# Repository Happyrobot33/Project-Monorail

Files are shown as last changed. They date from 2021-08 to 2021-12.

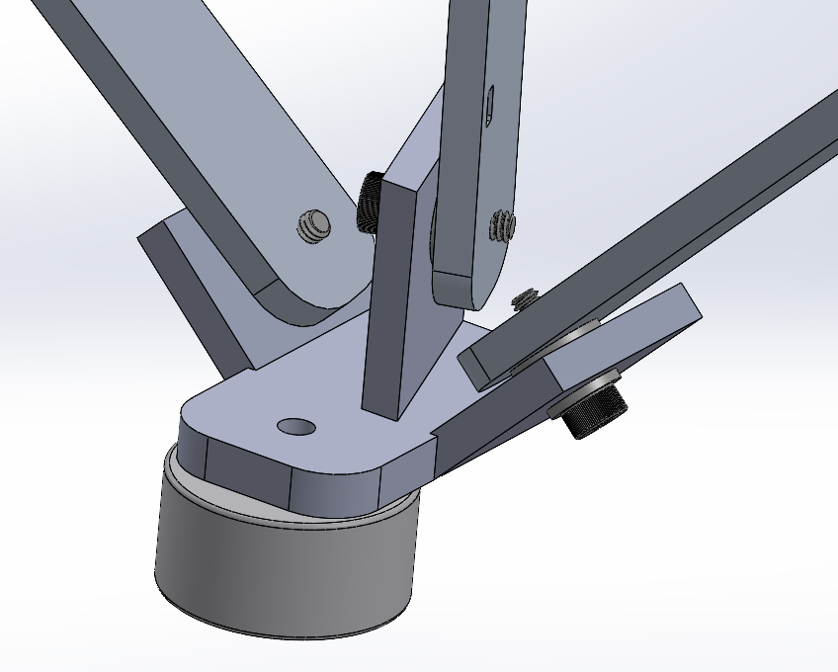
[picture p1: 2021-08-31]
CAD/Development Images/holy fuck.PNG

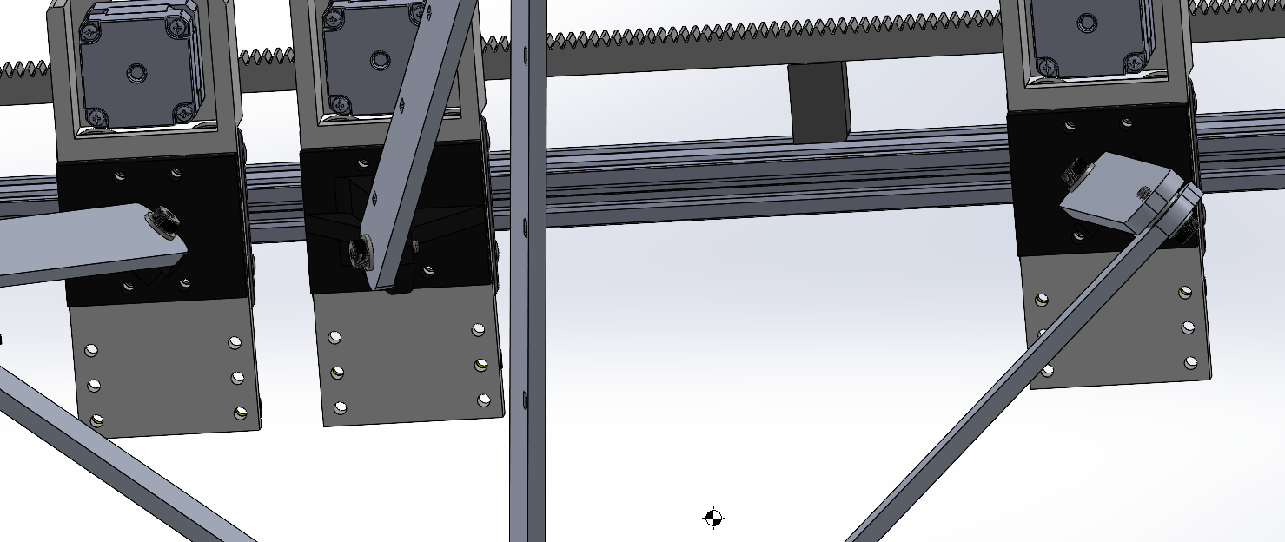
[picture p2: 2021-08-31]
CAD/Development Images/New Mounts.PNG

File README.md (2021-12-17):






# Project-Monorail
Project Monorail is an attempt to recreate a design shown by Nicholas Seward (https://www.youtube.com/watch?v=oBBhVcemVHc&amp;t=26s) that uses 1 linear rail to accomplish 3 dimensional movement

Use this to visualize if a point is reachable or not to prevent issues:
https://editor.p5js.org/Happyrobot33/sketches/HqeGeLe6U

https://user-images.githubusercontent.com/32679887/117662900-11516d00-b16e-11eb-9a66-542f85682d6e.mp4

https://user-images.githubusercontent.com/32679887/118267545-3d306380-b48a-11eb-8856-cf8bc8f9db5a.mp4

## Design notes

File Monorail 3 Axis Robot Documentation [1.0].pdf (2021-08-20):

# Monorail 3 Axis Robot Documentation

## Written and Designed by Matthew Herber

## Index: Pin Reservations Custom Expansion Board Diagram Custom Firmware Command Set Sample Program Basic Code Loop Explanation

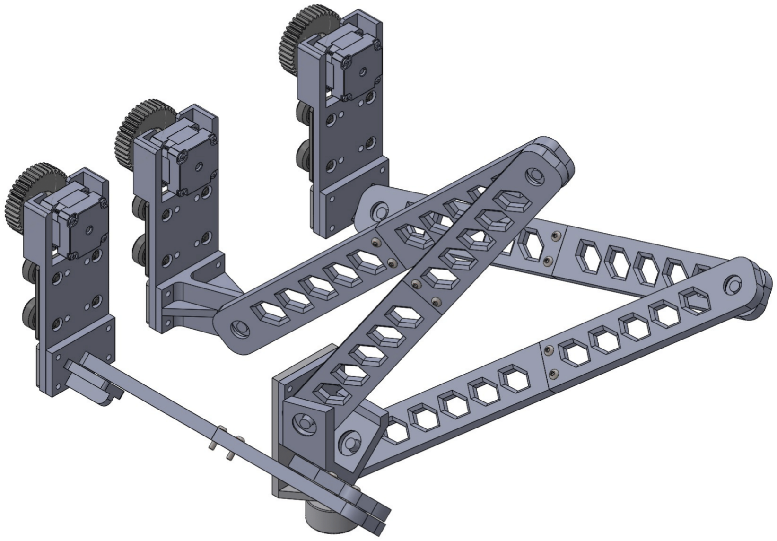
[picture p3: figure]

## REV 1.0 (8/19/2021) Page: 1

## Pin Reservations

Stepper 1
Data: D22, D23, D24, D25
Endstop: D34

Stepper 2
Data: D26, D27, D28, D29
Endstop: D35

Stepper 3
Data: D30, D31, D32, D33
Endstop: D36

Other:
Electromagnet: D37

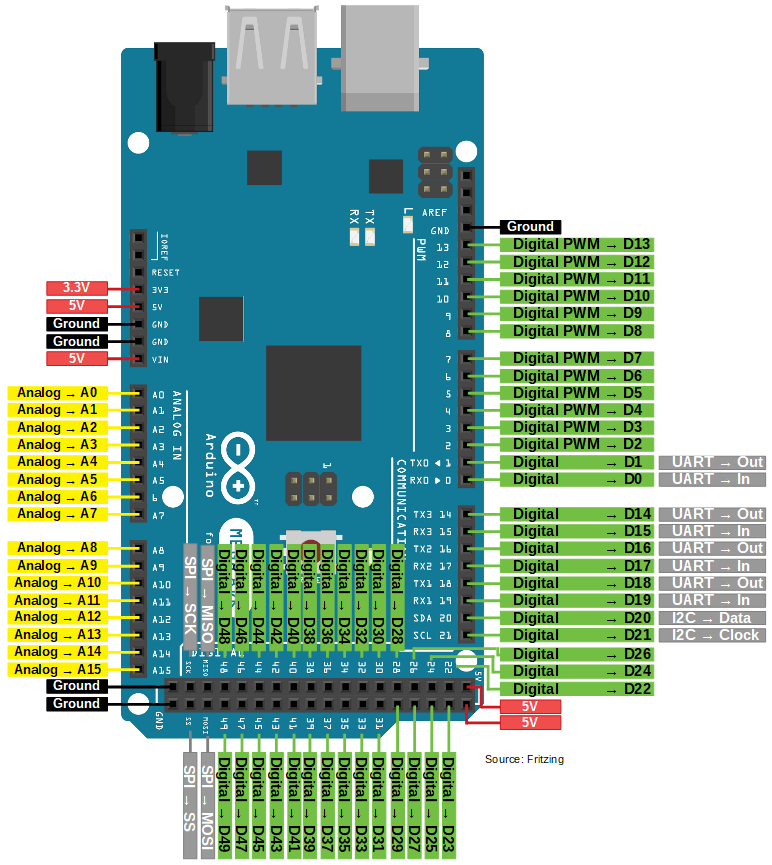
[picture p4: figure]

## REV 1.0 (8/19/2021) Page: 2

## Custom Expansion Board Diagram (Board Revision 3.0)

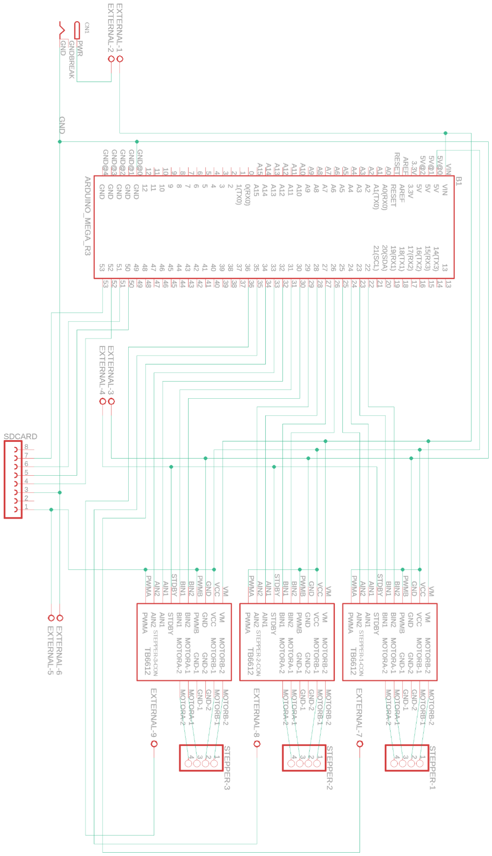
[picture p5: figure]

## REV 1.0 (8/19/2021) Page: 3

## Custom Firmware Command Set

Use # to indicate a comment on said line. To end a line, use ;\. All position commands use MM unless otherwise specified

lmove(x,y,z)
Moves the robot EOAT to the specified X Y Z coordinates in a straight line

jmove(x,y,z)
Moves the robot EOAT to the specified X Y Z coordinates as quick as possible

delay(ms)
Halts program execution for a specified amount of milliseconds

speed(%)
Sets the speed of the robot based on a percentage of the max speed. This change affects all motion moves after it is called

accel(%)
Sets the acceleration of the robot based on a percentage of the max acceleration. This change affects all motion moves after it is called

Carc(x,y,z,r,startAngle,endAngle)
Does a clockwise arc move given a center position, a radius from that center, a start angle and an end angle. always make sure your end angle is larger than your start angle

CCarc(x,y,z,r,startAngle,endAngle)
Does a counter-clockwise arc move given a center position, a radius from that center, a start angle and an end angle. always make sure your end angle is larger than your start angle

EOAT(0/1)
Turns on or off the EOAT, 0 for off and 1 for on

## REV 1.0 (8/19/2021) Page: 4

## Sample Program

### String program = "\ #basic starting program for testing;\ jmove(550,200,100);\ delay(1000);\ jmove(50,50,25);\ jmove(500,50,5);\ jmove(200,100,100);\ jmove(0,0,0);\ delay(1000);\ EOAT(1);\

;\

### Section to test speed command;\ speed(20);\ lmove(300,200,300);\ speed();\ lmove(0,0,0);\ EOAT(0);\

;\

### Section to test accel command;\ delay(1000);\ accel(5);\ lmove(300,200,300);\ accel();\ lmove(0,0,0);\ delay(1000);\ EOAT(1);\ #Rapid section testing individual axis moves;\

#X;\

### lmove(200,0,0);\ delay(1000);\ jmove(100,0,0);\

## REV 1.0 (8/19/2021) Page: 5

## Sample Program (cont)

#Y;\

### lmove(100,100,0);\ delay(1000);\ jmove(100,0,0);\

#Z;\

### lmove(100,0,100);\ delay(1000);\ jmove(100,0,0);\ #ALL AXIS;\ lmove(400,50,200);\ delay(1000);\ jmove(100,0,0);\ #Arc Testing;\ Carc(400,200,0,200,360,0);\ lmove(0,0,0);\ CCarc(400,200,0,200,0,360);\ lmove(0,0,0);\ EOAT(0);\

";

## REV 1.0 (8/19/2021) Page: 6

## Basic Code Loop Explanation

The execution of the custom firmware is actually quite simple. There is a string variable stored internally to the code, that contains the entire program. This is done so that in later revisions strings can be read in from a storage device to have different programs stored without requiring a reflash of the Arduino itself. This string is then converted into an array of instructions, using ;\ as a line end marker. This array is looped over for each instruction.

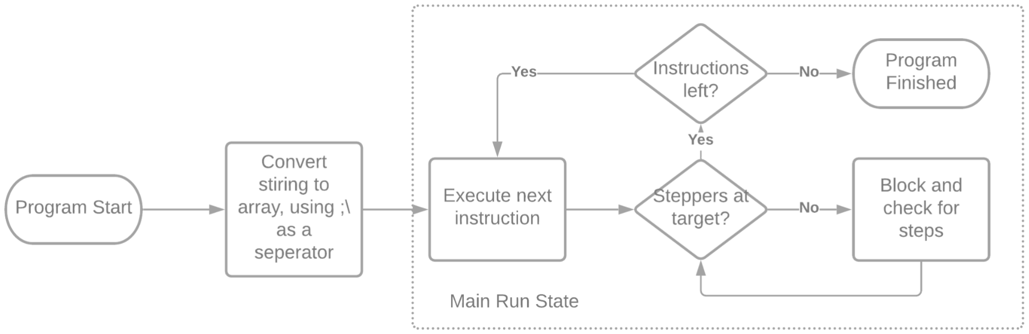
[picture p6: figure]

## REV 1.0 (8/19/2021) Page: 7

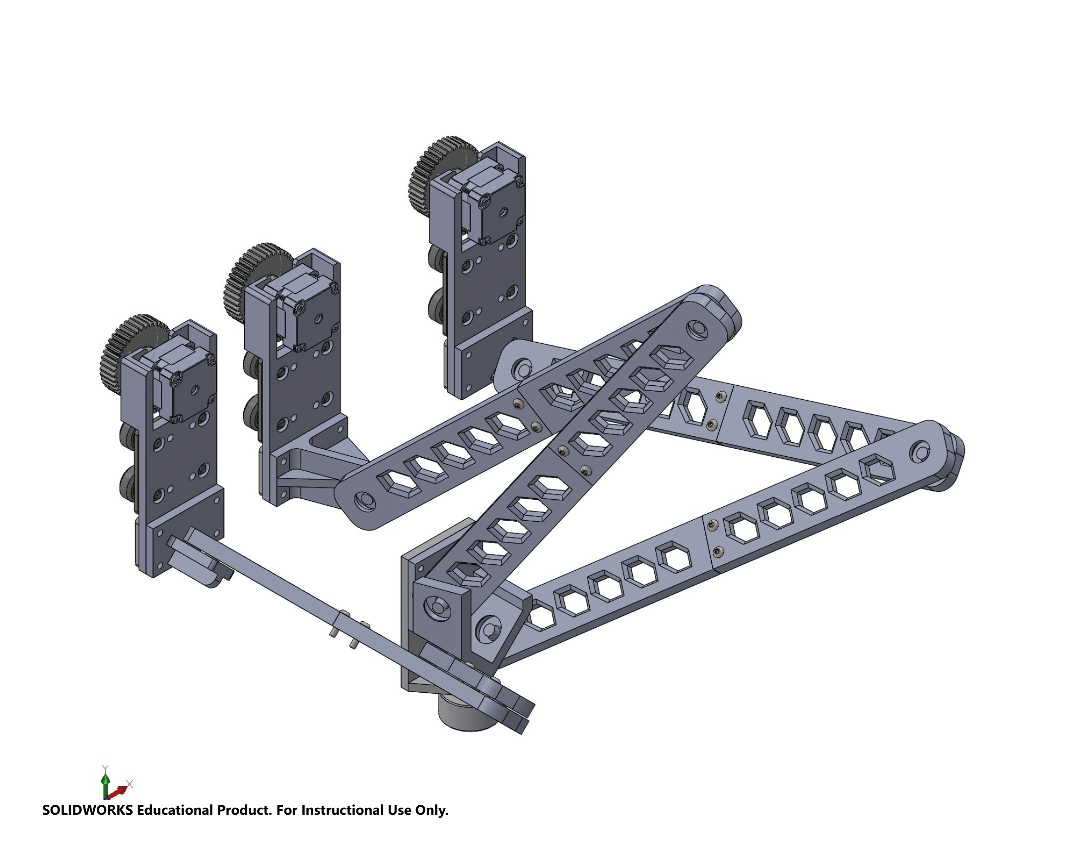
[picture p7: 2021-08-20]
Cover Image-1.png

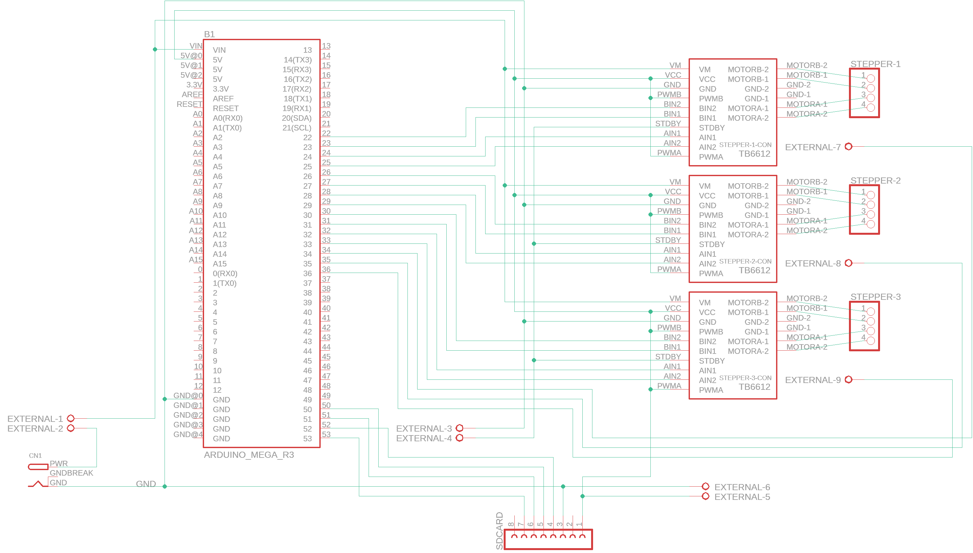
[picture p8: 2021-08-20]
rev 3 diagram.png

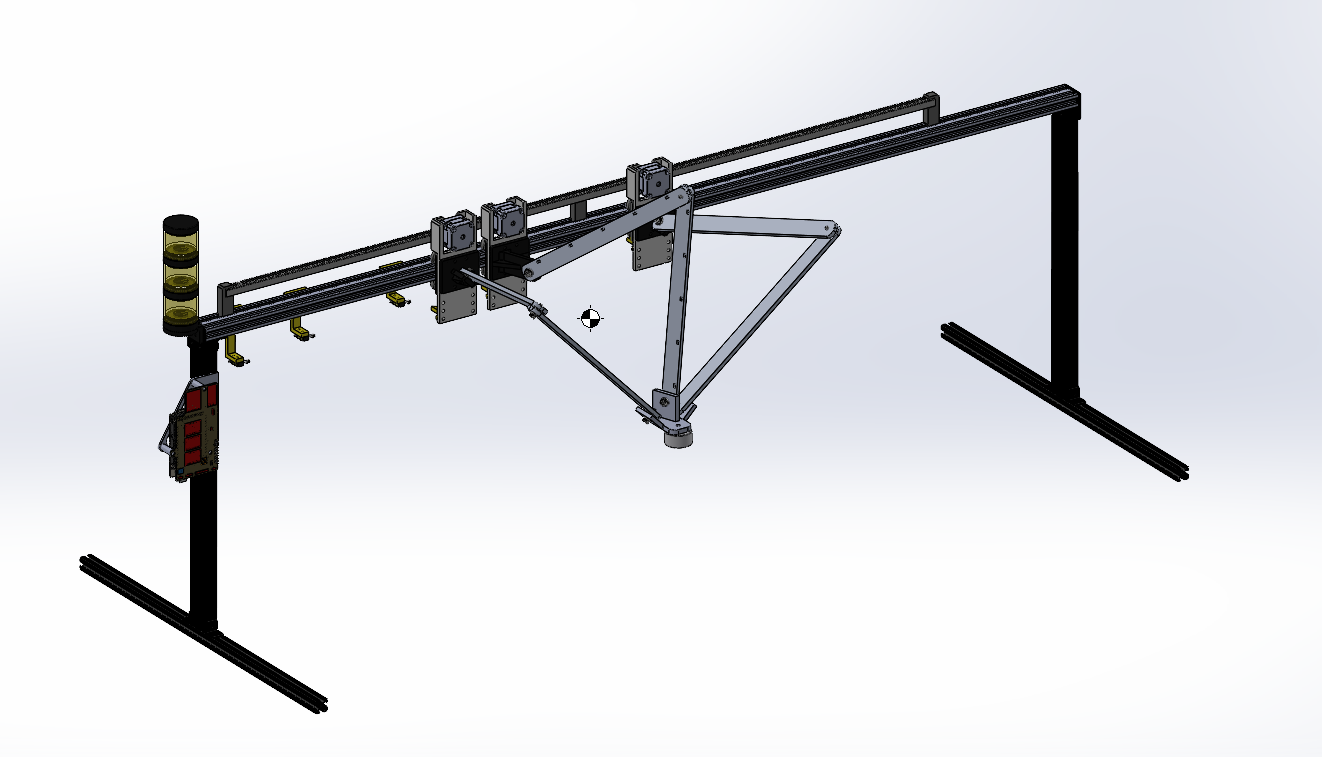
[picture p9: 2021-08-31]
CAD/Development Images/Full Image.PNG

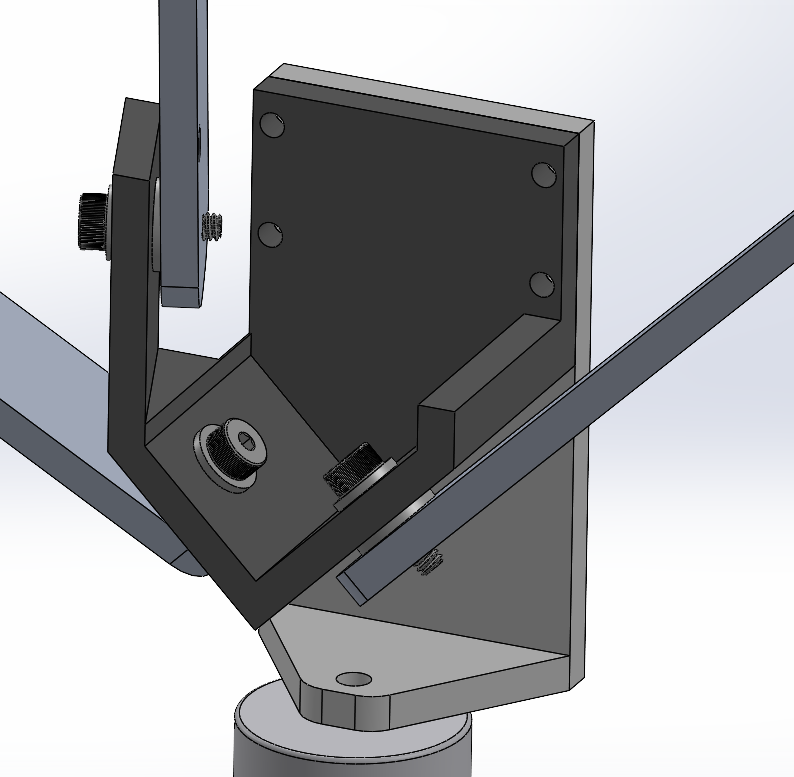
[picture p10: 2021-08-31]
CAD/Development Images/help.PNG

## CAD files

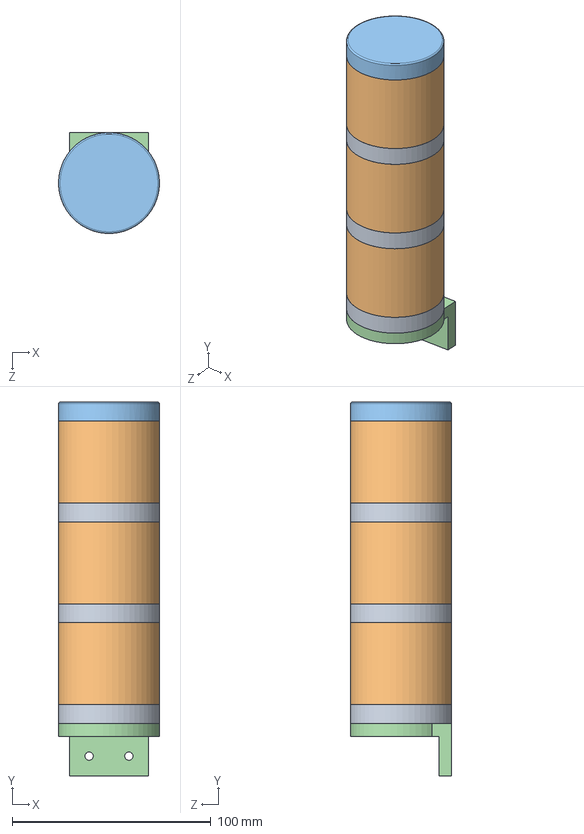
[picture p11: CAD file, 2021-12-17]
CAD/A600 Misc/Light Stack.SLDASM
50.8 x 188.3 x 50.8 mm
Light Stack Seperator x 3
Light Stack Diffuser x 3
Light Stack Cap
Light Stack Base

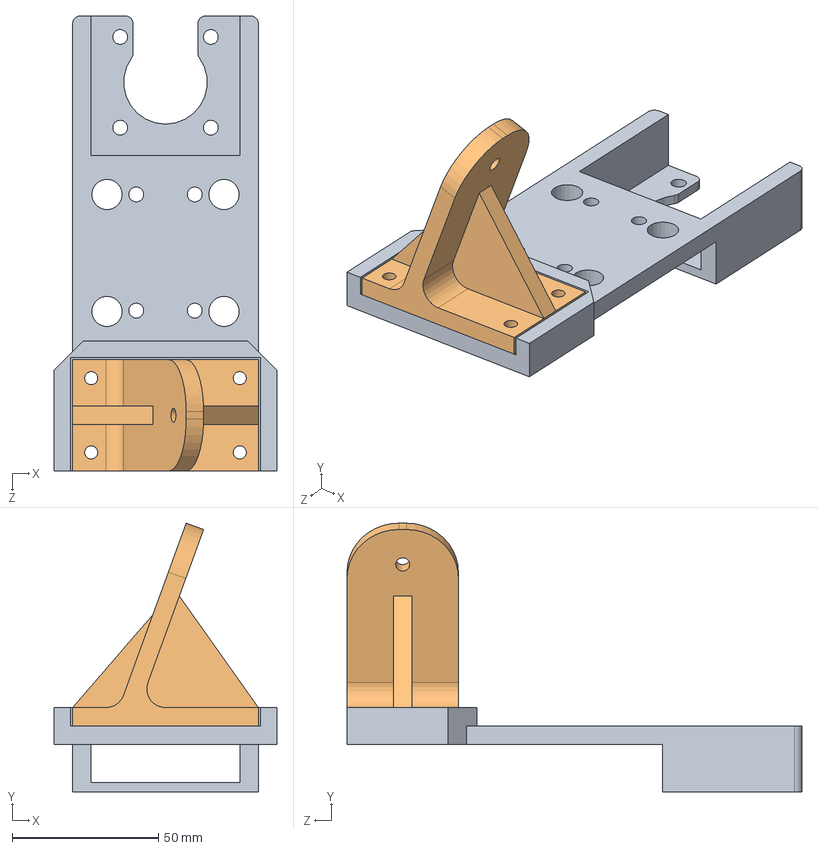
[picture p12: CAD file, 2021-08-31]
CAD/FEA Assembly.SLDASM
76.2 x 91.9 x 155.6 mm
Slide Casing
Inner Mount

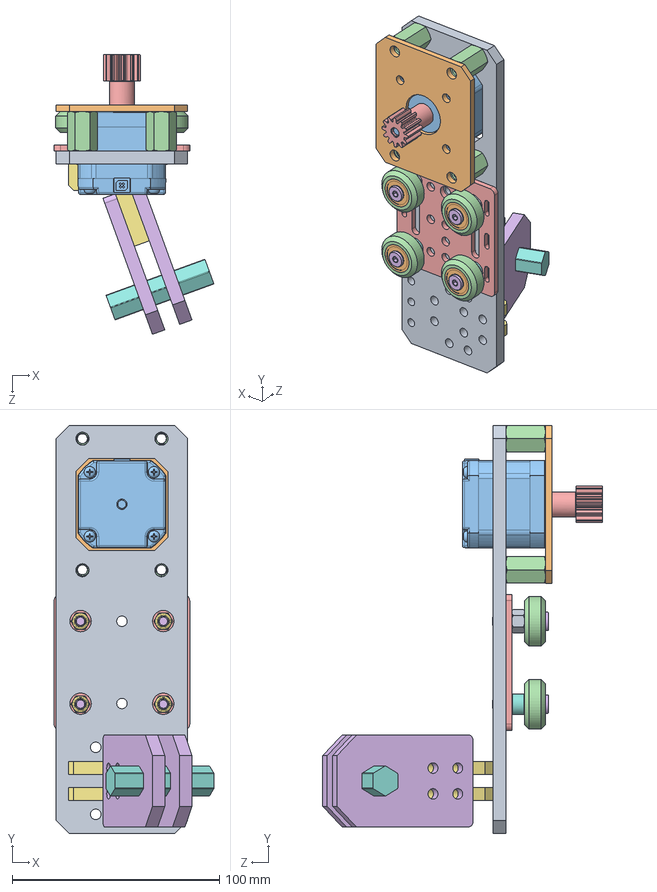
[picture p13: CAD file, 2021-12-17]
CAD/A200 Cart/A200 Cart.SLDASM
77.1 x 196.8 x 134.9 mm
A201 Cart Mount Plate
A202 Cart Stepper Plate
6627T67_Position-Control DC Motor
91780A357_Female Threaded Hex Standoff x 4
V-Slot Gantry Plate 20mm.step
Low Profile Screw M5 v1.step x 4
Nylon Insert Lock Nut M5.step x 4
Aluminum Spacer 6mm.step x 2
Eccentric Spacer 6mm v1.step x 2
Ball Bearing 5 x 16 x 5.step x 8
Precision Shim 8 x 5 x 1.step x 4
Xtreme Solid V Wheel.step x 4
5172T160_HT-LOAD MTL GEAR--20 DEG PRESSURE ANGLE
A204 Outer Mount Bearing Plate x 2
A203 Inner Mount Angle Bracket x 2
1_2 OD Hex Stock (18) (217-3309)^A200 Cart

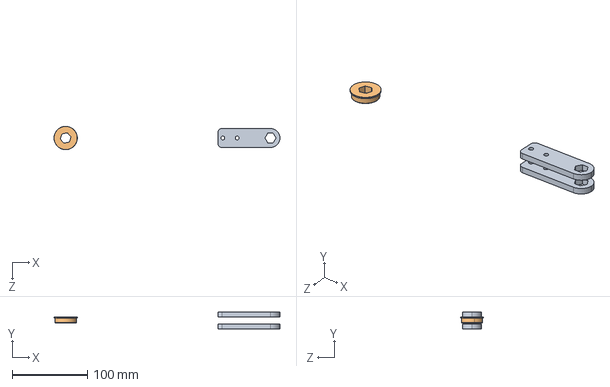
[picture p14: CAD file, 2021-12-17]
CAD/A400 Link/A400 Link.SLDASM
301.3 x 22.2 x 31.1 mm
A402 Bar Clevis Plate x 2
am-2986 FR8ZZ Hex Bearing.step

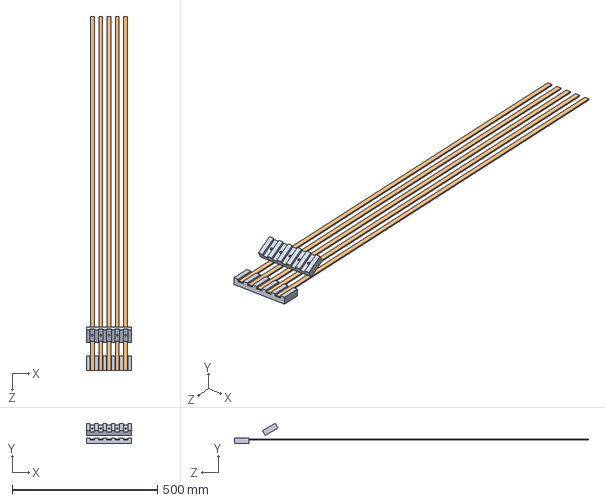
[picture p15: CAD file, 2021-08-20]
CAD/A300 Rail/Bus Bar Concept.SLDASM
155.6 x 70.5 x 1219.2 mm
Bus Bar Holder x 2
Copper Bus Bar x 5

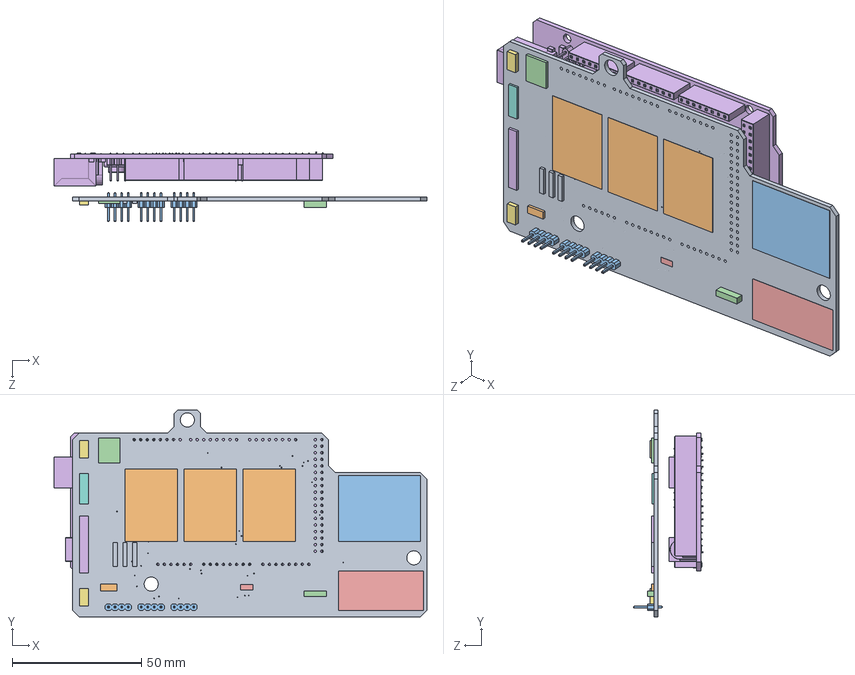
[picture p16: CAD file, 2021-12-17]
CAD/A600 Misc/Board.SLDASM
144.3 x 80.0 x 26.9 mm
Board.step
TB6612-BREAKOUT-MOTOR-CONTROLLER.step x 3
1X04.step x 3
DCJACK_2MM_PTH.step
NRF24L01_RF_MODULE.step
W237-5P.step
W237-132.step x 2
W237-3E.step
220 Ω.step x 3
2N2222.step
MICRO_SD_BREAKOUT.step
F_QMX.step
CLEAR.step
ArduinoMega_IGES.igs

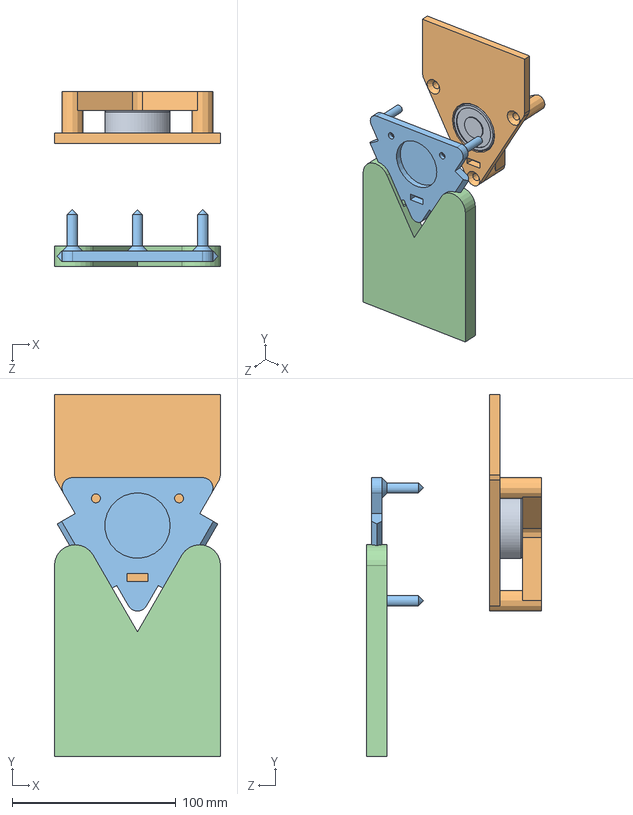
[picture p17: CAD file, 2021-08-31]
CAD/A500 Head/ATC Example Usage.SLDASM
101.6 x 221.3 x 107.2 mm
25kg electromagnet
ATC
ATC Tool Mount
ATC Tool Holder

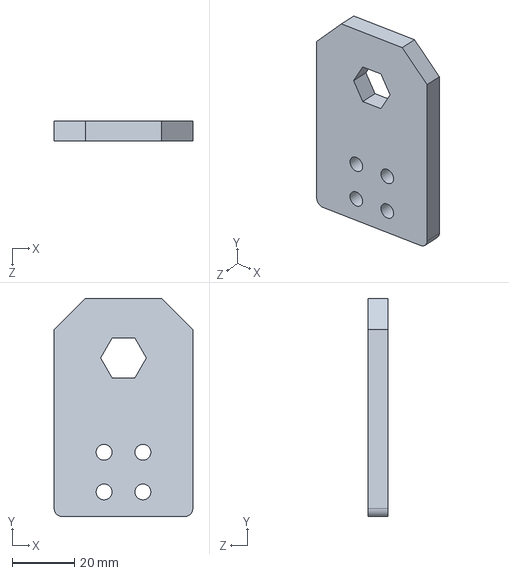
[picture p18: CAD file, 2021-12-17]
CAD/A200 Cart/A204 Outer Mount Bearing Plate.SLDPRT
44.5 x 69.8 x 6.35 mm

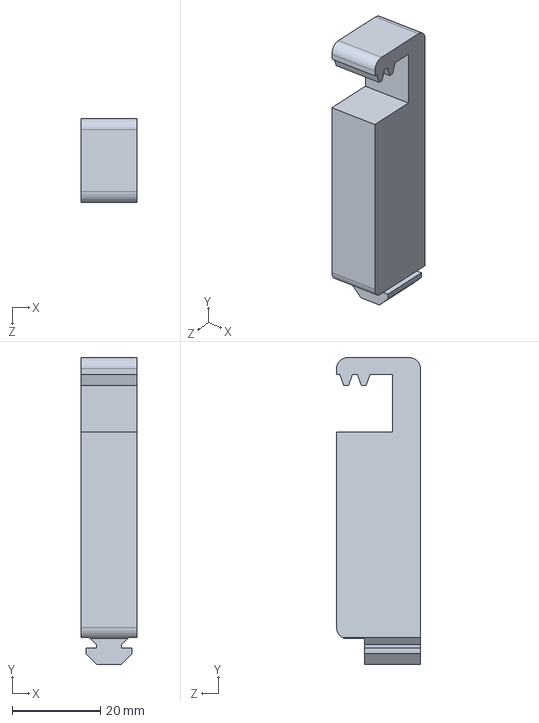
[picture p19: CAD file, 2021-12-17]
CAD/A300 Rail/Temporary Gear Mount.SLDPRT
12.7 x 69.6 x 19.1 mm

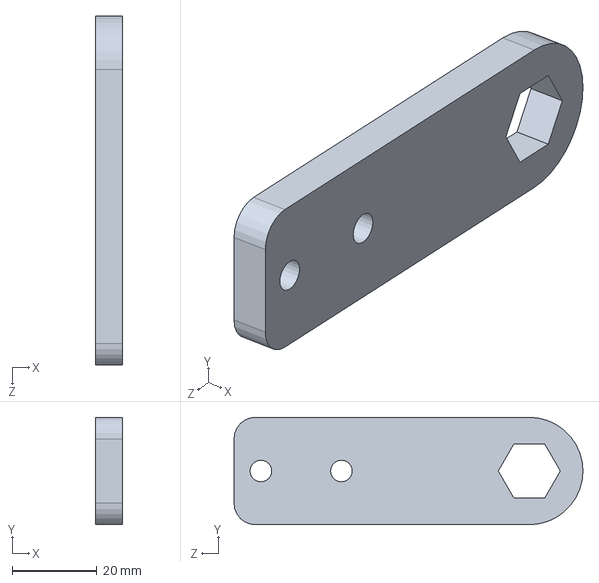
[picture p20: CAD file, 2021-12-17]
CAD/A400 Link/A402 Bar Clevis Plate.SLDPRT
6.35 x 25.4 x 82.5 mm

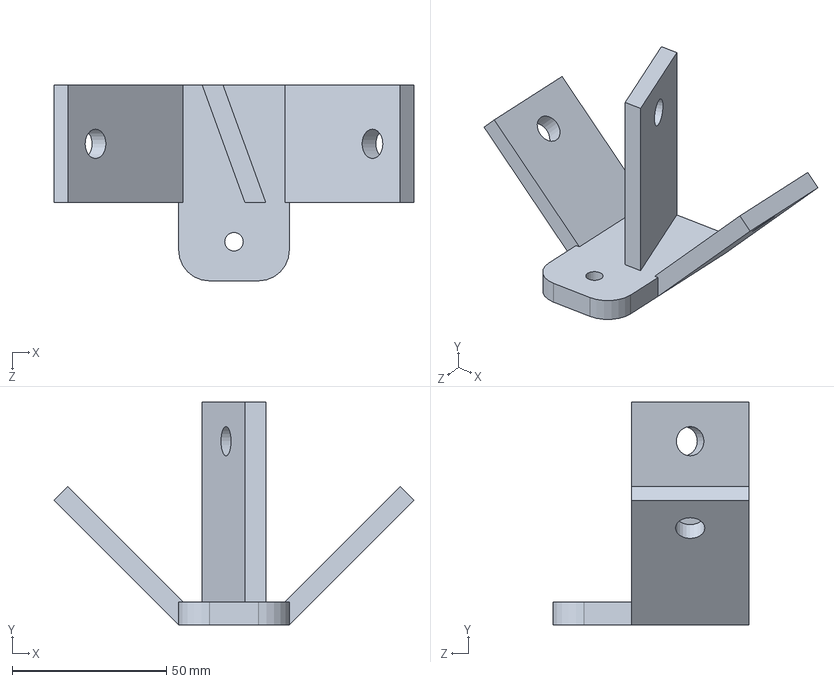
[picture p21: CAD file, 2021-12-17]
CAD/A500 Head/Head v2.SLDPRT
116.7 x 72.3 x 63.5 mm

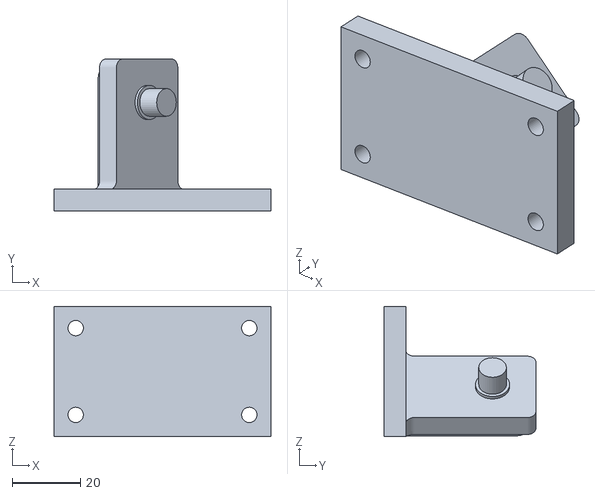
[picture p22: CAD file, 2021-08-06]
STL/Outer Mounts Default.STL
63.5 x 44.5 x 38.1

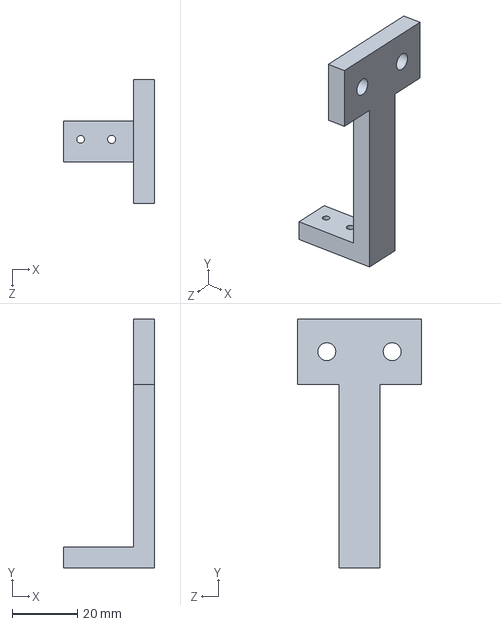
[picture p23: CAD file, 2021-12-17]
CAD/A300 Rail/MicroSwitch Under Mount.SLDPRT
27.8 x 76.2 x 38.1 mm

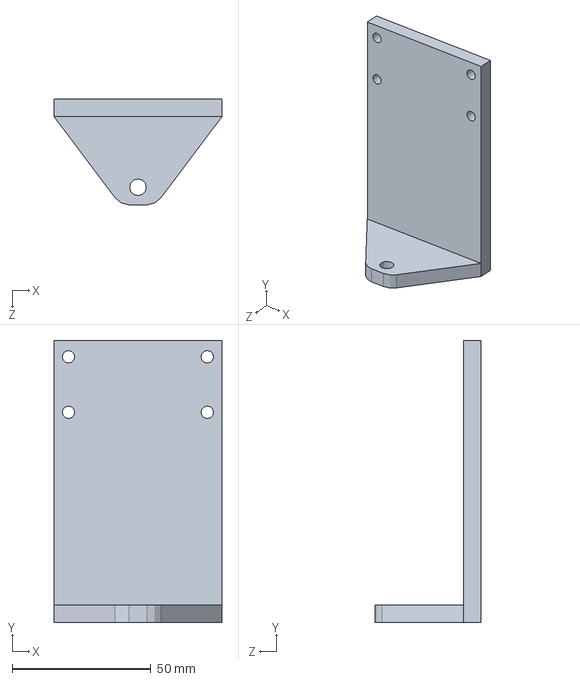
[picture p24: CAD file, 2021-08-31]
CAD/A500 Head/Electromagnet EOAT.SLDPRT
60.5 x 101.6 x 38.1 mm

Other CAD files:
Render/Head.PLY
CAD/A600 Misc/Light Stack Diffuser.SLDPRT
CAD/Triangle Calculations.SLDPRT
Render/Extrusion.PLY
CAD/A200 Cart/A201 Cart Mount Plate.SLDPRT
CAD/A200 Cart/A202 Cart Stepper Plate.SLDPRT
CAD/A200 Cart/A203 Inner Mount Angle Bracket.SLDPRT
CAD/A200 Cart/Cart Mount Plate.DXF
CAD/A200 Cart/Cart Stepper Plate.DXF
CAD/A200 Cart/Inner Mount Angle Bracket.DXF
CAD/A200 Cart/Outer Mount Bearing Plate.DXF
CAD/A300 Rail/Bus Bar Holder.SLDPRT
CAD/A300 Rail/Copper Bus Bar.SLDPRT
CAD/A400 Link/A401 Aluminum Bar.SLDPRT
CAD/A400 Link/Bar Clevis Plate.DXF
CAD/A500 Head/ATC Tool Holder.SLDPRT
CAD/A500 Head/ATC Tool Mount.SLDPRT
CAD/A500 Head/ATC.SLDPRT
CAD/A500 Head/Head.SLDPRT
CAD/A600 Misc/Board Mount.SLDPRT
CAD/A600 Misc/Light Stack Base.SLDPRT
CAD/A600 Misc/Light Stack Cap.SLDPRT
CAD/A600 Misc/Light Stack Seperator.SLDPRT
CAD/OLD/Bar.SLDPRT
CAD/OLD/Bearing Fit Test Internal.SLDPRT
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

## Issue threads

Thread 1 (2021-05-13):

No arc commands

Happyrobot33, 2021-05-13:
No arc / circle commands are present. Here is a proposal for that: https://www.desmos.com/calculator/zzamiibnki

Happyrobot33, 2021-05-14:
Arc commands added in fff759550248dae4620b4c08fd9e4bcf71ba2048, but issues are still present so this is still a problem. commands disabled in a52cebe1a37ab307f21e28994de08a783c661ccf. Plan to fix in coming days

Happyrobot33, 2021-05-18:
Arc commands seem to work, however due to #2, if this is true or not is currently unknown

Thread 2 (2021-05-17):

Very jittery and y axis is very imprecise

Happyrobot33, 2021-05-17:
This is likely due to multiple factors adding up on eachother, for one being the current arms are only 7 inches long. another is that the arms are quite thin, and the mounts also have alot of give. hoping to fix these things soon.

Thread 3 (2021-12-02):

Gear Rack Mount not final version

Happyrobot33, 2021-12-02:
Current Gear rack mounting solution does not allow for additional racks. Final version should use something that allows for additional racks to be added

Happyrobot33, 2022-10-31:
Solved with gear rack being moved to the back

Closed 2022-10-31.

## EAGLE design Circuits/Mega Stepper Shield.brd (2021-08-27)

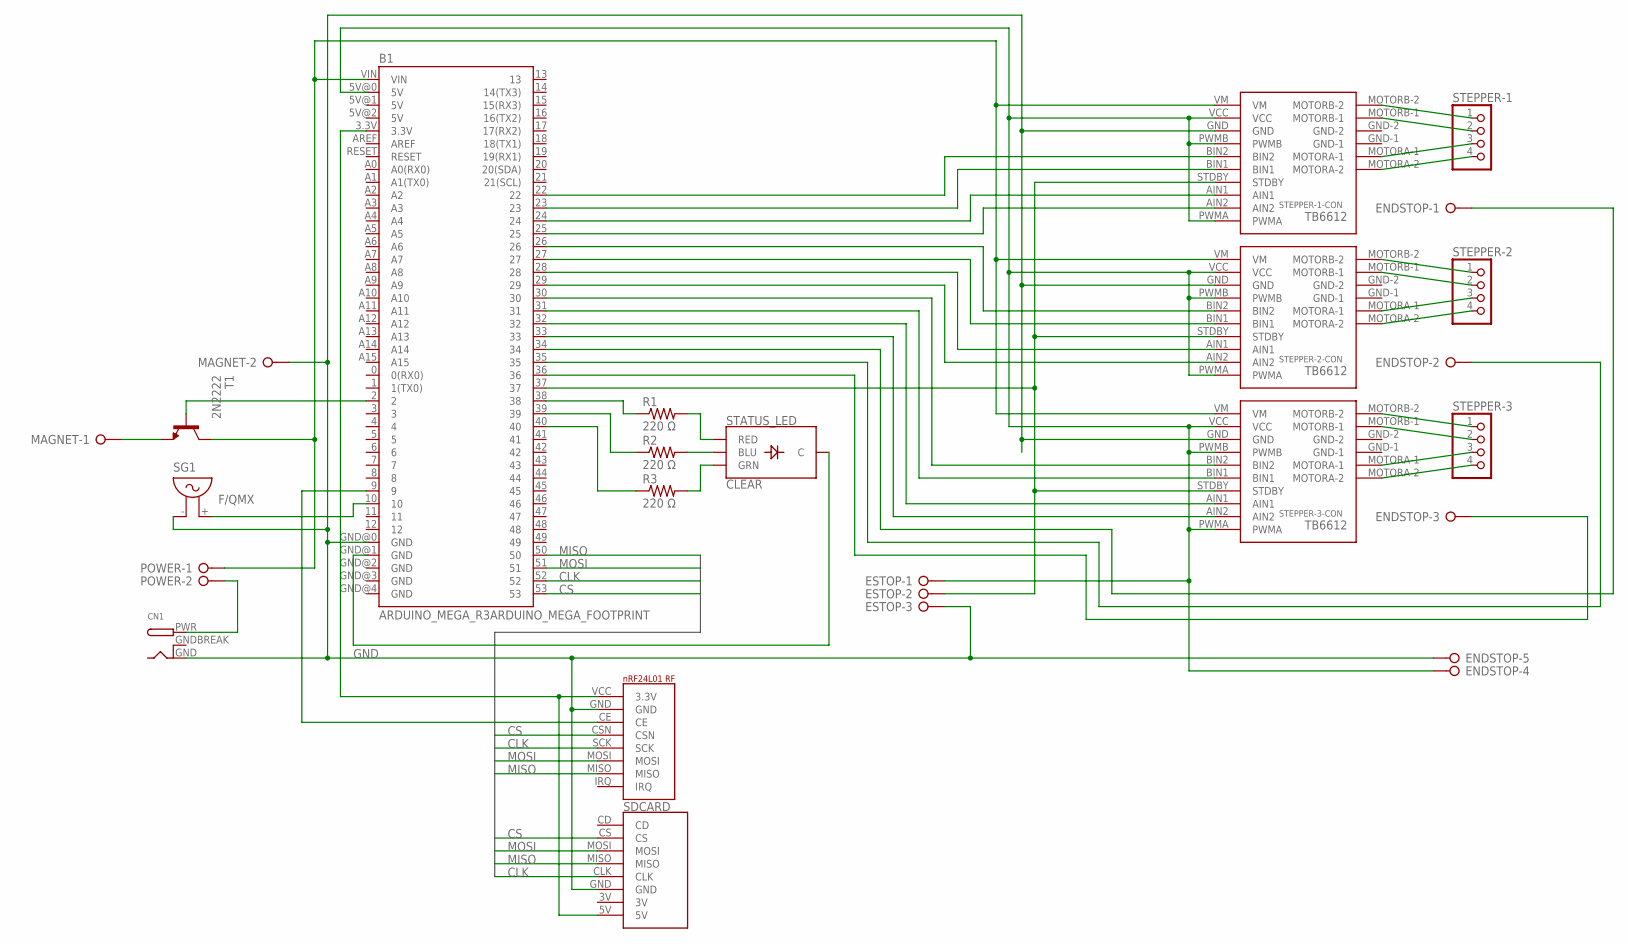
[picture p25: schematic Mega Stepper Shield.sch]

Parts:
B1: ARDUINO_MEGA_R3ARDUINO_MEGA_FOOTPRINT; ARDUINO_MEGA_SHIELD_DIMENSIONLESS
CN1: DCBARRELPTH; DCJACK_2MM_PTH
ENDSTOP: W237-05P; W237-5P
ESTOP: W237-3E
MAGNET: W237-02P; W237-132
POWER: W237-02P; W237-132
R1, R2, R3: 220 Ω; 0204/7
SDCARD: MICRO_SD_BREAKOUT; MICROSDCARDBREAKOUT
SG1: F/QMX
STATUS_LED: CLEAR; LED-RGB-THRU
STEPPER-1, STEPPER-2, STEPPER-3: PINHD-1X4; 1X04
STEPPER-1-CON, STEPPER-2-CON, STEPPER-3-CON: TB6612-BREAKOUT-MOTOR-CONTROLLER; TB6612-HEADERS
T1: 2N2222; TO92-EBC-OVAL
U$1: NRF24L01_RF_MODULE; NRF24L01RF

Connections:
3.3V: B1.3.3V, SDCARD.5V, U$1.VCC (3.3V)
5V: B1.5V@0 (5V), ENDSTOP.4, ESTOP.1, STEPPER-1-CON.PWMA, STEPPER-1-CON.PWMB, STEPPER-1-CON.VCC, STEPPER-2-CON.PWMA, STEPPER-2-CON.PWMB, STEPPER-2-CON.VCC, STEPPER-3-CON.PWMA, STEPPER-3-CON.PWMB, STEPPER-3-CON.VCC
12V10A: B1.VIN, POWER.1, STEPPER-1-CON.VM, STEPPER-2-CON.VM, STEPPER-3-CON.VM, T1.C
AIN1: B1.24, STEPPER-1-CON.AIN1
AIN2: B1.25, STEPPER-1-CON.AIN2
BIN2: B1.22, STEPPER-1-CON.BIN2
CLK: B1.52, SDCARD.CLK, U$1.SCK
CS: B1.53, SDCARD.CS, U$1.CSN
GND: B1.GND@0 (GND), CN1.GND, ENDSTOP.5, ESTOP.3, MAGNET.2, SDCARD.GND, SG1.- (1), STEPPER-1-CON.GND, STEPPER-2-CON.GND, STEPPER-3-CON.GND, U$1.GND
GNDBREAK: CN1.GNDBREAK
MISO: B1.50, SDCARD.MISO, U$1.MISO
MOSI: B1.51, SDCARD.MOSI, U$1.MOSI
unnamed: B1.36, ENDSTOP.3
unnamed: B1.10, SG1.+ (2)
unnamed: B1.30, STEPPER-3-CON.BIN2
unnamed: B1.26, STEPPER-2-CON.BIN2
unnamed: B1.27, STEPPER-2-CON.BIN1
unnamed: B1.28, STEPPER-2-CON.AIN1
unnamed: B1.29, STEPPER-2-CON.AIN2
unnamed: B1.31, STEPPER-3-CON.BIN1
unnamed: B1.32, STEPPER-3-CON.AIN1
unnamed: B1.33, STEPPER-3-CON.AIN2
unnamed: CN1.PWR, POWER.2
unnamed: B1.35, ENDSTOP.2
unnamed: B1.37, ESTOP.2, STEPPER-1-CON.STDBY, STEPPER-2-CON.STDBY, STEPPER-3-CON.STDBY
unnamed: B1.34, ENDSTOP.1
unnamed: STEPPER-1.1, STEPPER-1-CON.MOTORB-2
unnamed: STEPPER-1.2, STEPPER-1-CON.MOTORB-1
unnamed: STEPPER-1.3, STEPPER-1-CON.MOTORA-1
unnamed: STEPPER-1.4, STEPPER-1-CON.MOTORA-2
unnamed: STEPPER-2.1, STEPPER-2-CON.MOTORB-2
unnamed: STEPPER-2.2, STEPPER-2-CON.MOTORB-1
unnamed: STEPPER-2.3, STEPPER-2-CON.MOTORA-1
unnamed: STEPPER-2.4, STEPPER-2-CON.MOTORA-2
unnamed: STEPPER-3.1, STEPPER-3-CON.MOTORB-2
unnamed: STEPPER-3.2, STEPPER-3-CON.MOTORB-1
unnamed: STEPPER-3.3, STEPPER-3-CON.MOTORA-1
unnamed: STEPPER-3.4, STEPPER-3-CON.MOTORA-2
unnamed: B1.23, STEPPER-1-CON.BIN1
unnamed: R3.2, STATUS_LED.3 (GRN)
unnamed: R2.2, STATUS_LED.4 (BLU)
unnamed: R1.2, STATUS_LED.1 (RED)
unnamed: B1.GND@1 (GND), STATUS_LED.2 (C)
unnamed: B1.9, U$1.CE
unnamed: B1.38, R1.1
unnamed: B1.39, R2.1
unnamed: B1.40, R3.1
unnamed: B1.2, T1.B
unnamed: MAGNET.1, T1.E

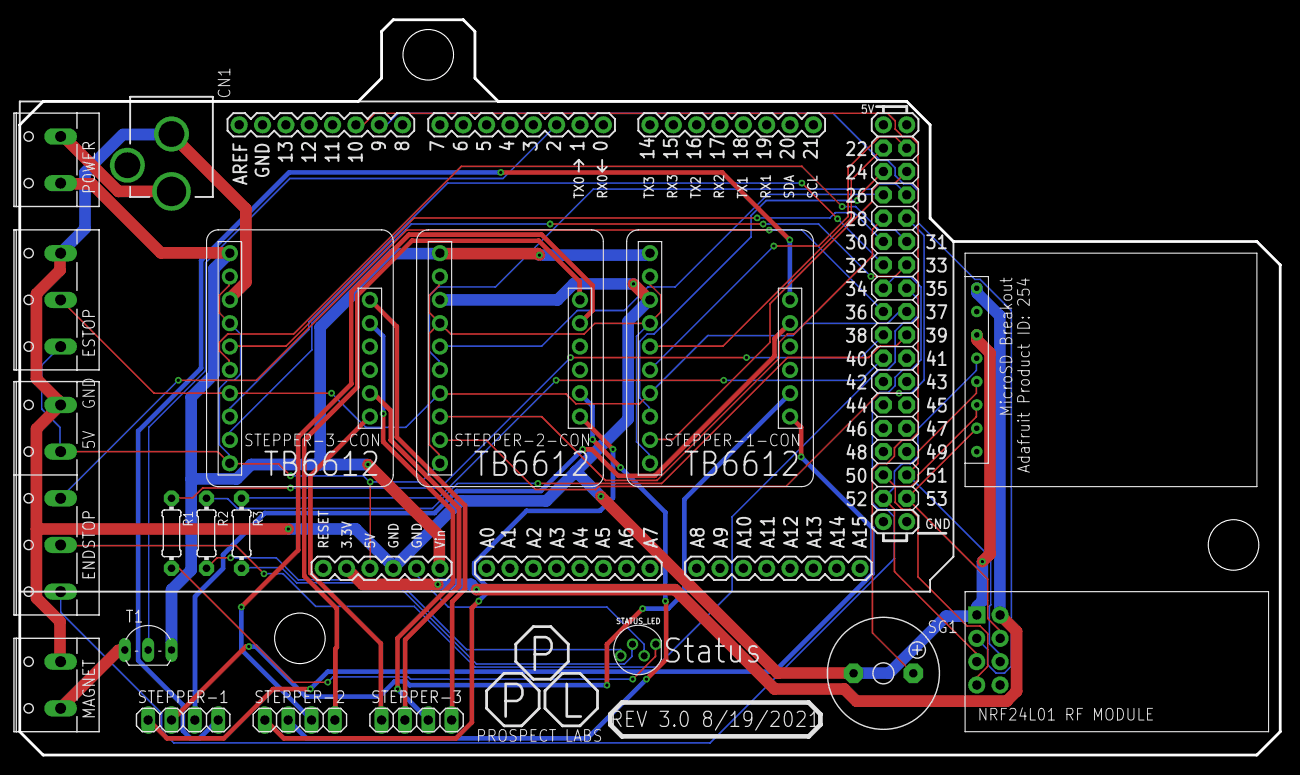
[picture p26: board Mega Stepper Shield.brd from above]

Board: 2 copper layers, 137.2 x 80.0 mm, 20 parts (0 on the bottom side), 48 nets.

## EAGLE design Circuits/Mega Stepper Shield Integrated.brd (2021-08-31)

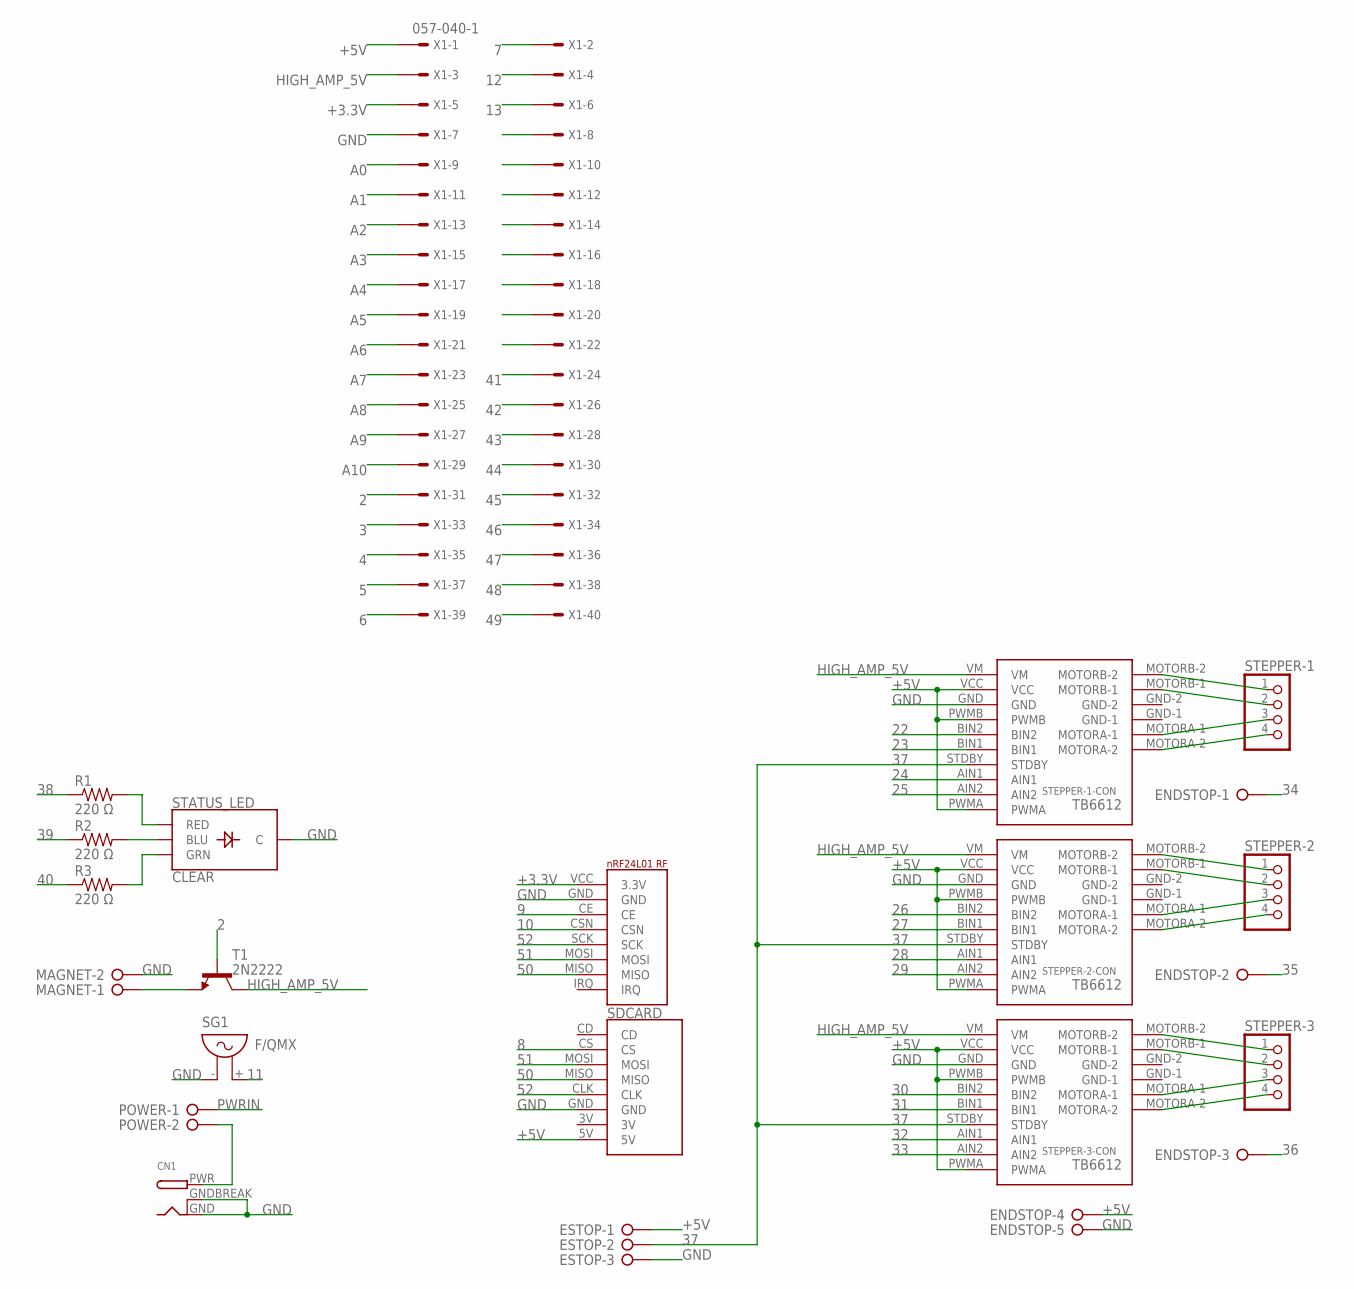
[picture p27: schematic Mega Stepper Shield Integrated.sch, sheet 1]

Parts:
CN1: DCBARRELPTH; DCJACK_2MM_PTH
ENDSTOP: W237-05P; W237-5P
ESTOP: W237-3E
MAGNET: W237-02P; W237-132
POWER: W237-02P; W237-132
R1, R2, R3: 220 Ω; 0204/7
SDCARD: MICRO_SD_BREAKOUT; MICROSDCARDBREAKOUT
SG1: F/QMX
STATUS_LED: CLEAR; LED-RGB-THRU
STEPPER-1, STEPPER-2, STEPPER-3: PINHD-1X4; 1X04
STEPPER-1-CON, STEPPER-2-CON, STEPPER-3-CON: TB6612-BREAKOUT-MOTOR-CONTROLLER; TB6612-HEADERS
T1: 2N2222; TO92-EBC-OVAL
U$1: NRF24L01_RF_MODULE; NRF24L01RF
X1: 057-040-1

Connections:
2: T1.B, X1.31; also elsewhere on the board
3: X1.33; also elsewhere on the board
4: X1.35; also elsewhere on the board
5: X1.37; also elsewhere on the board
6: X1.39; also elsewhere on the board
7: X1.2; also elsewhere on the board
8: SDCARD.CS; also elsewhere on the board
9: U$1.CE; also elsewhere on the board
10: U$1.CSN; also elsewhere on the board
11: SG1.+ (2); also elsewhere on the board
12: X1.4; also elsewhere on the board
13: X1.6; also elsewhere on the board
16: X1.8
22: STEPPER-1-CON.BIN2; also elsewhere on the board
23: STEPPER-1-CON.BIN1; also elsewhere on the board
24: STEPPER-1-CON.AIN1; also elsewhere on the board
25: STEPPER-1-CON.AIN2; also elsewhere on the board
26: STEPPER-2-CON.BIN2; also elsewhere on the board
27: STEPPER-2-CON.BIN1; also elsewhere on the board
28: STEPPER-2-CON.AIN1; also elsewhere on the board
29: STEPPER-2-CON.AIN2; also elsewhere on the board
30: STEPPER-3-CON.BIN2; also elsewhere on the board
31: STEPPER-3-CON.BIN1; also elsewhere on the board
32: STEPPER-3-CON.AIN1; also elsewhere on the board
33: STEPPER-3-CON.AIN2; also elsewhere on the board
34: ENDSTOP.1; also elsewhere on the board
35: ENDSTOP.2; also elsewhere on the board
36: ENDSTOP.3; also elsewhere on the board
37: ESTOP.2, STEPPER-1-CON.STDBY, STEPPER-2-CON.STDBY, STEPPER-3-CON.STDBY; also elsewhere on the board
38: R1.1; also elsewhere on the board
39: R2.1; also elsewhere on the board
40: R3.1, X1.22; also elsewhere on the board
41: X1.24; also elsewhere on the board
42: X1.26; also elsewhere on the board
43: X1.28; also elsewhere on the board
44: X1.30; also elsewhere on the board
45: X1.32; also elsewhere on the board
46: X1.34; also elsewhere on the board
47: X1.36; also elsewhere on the board
48: X1.38; also elsewhere on the board
49: X1.40; also elsewhere on the board
50: SDCARD.MISO, U$1.MISO; also elsewhere on the board
51: SDCARD.MOSI, U$1.MOSI; also elsewhere on the board
52: SDCARD.CLK, U$1.SCK; also elsewhere on the board
+3.3V: U$1.VCC (3.3V), X1.5
+5V: ENDSTOP.4, ESTOP.1, SDCARD.5V, STEPPER-1-CON.PWMA, STEPPER-1-CON.PWMB, STEPPER-1-CON.VCC, STEPPER-2-CON.PWMA, STEPPER-2-CON.PWMB, STEPPER-2-CON.VCC, STEPPER-3-CON.PWMA, STEPPER-3-CON.PWMB, STEPPER-3-CON.VCC, X1.1; also elsewhere on the board
A0: X1.9; also elsewhere on the board
A1: X1.11; also elsewhere on the board
A2: X1.13; also elsewhere on the board
A3: X1.15; also elsewhere on the board
A4: X1.17; also elsewhere on the board
A5: X1.19; also elsewhere on the board
A6: X1.21; also elsewhere on the board
A7: X1.23; also elsewhere on the board
A8: X1.25; also elsewhere on the board
A9: X1.27; also elsewhere on the board
A10: X1.29; also elsewhere on the board
GND: CN1.GND, CN1.GNDBREAK, ENDSTOP.5, ESTOP.3, MAGNET.2, SDCARD.GND, SG1.- (1), STATUS_LED.2 (C), STEPPER-1-CON.GND, STEPPER-2-CON.GND, STEPPER-3-CON.GND, U$1.GND, X1.7; also elsewhere on the board
HIGH_AMP_5V: STEPPER-1-CON.VM, STEPPER-2-CON.VM, STEPPER-3-CON.VM, T1.C, X1.3; also elsewhere on the board
unnamed: CN1.PWR, POWER.2
unnamed: STEPPER-1.1, STEPPER-1-CON.MOTORB-2
unnamed: STEPPER-1.2, STEPPER-1-CON.MOTORB-1
unnamed: STEPPER-1.3, STEPPER-1-CON.MOTORA-1
unnamed: STEPPER-1.4, STEPPER-1-CON.MOTORA-2
unnamed: STEPPER-2.1, STEPPER-2-CON.MOTORB-2
unnamed: STEPPER-2.2, STEPPER-2-CON.MOTORB-1
unnamed: STEPPER-2.3, STEPPER-2-CON.MOTORA-1
unnamed: STEPPER-2.4, STEPPER-2-CON.MOTORA-2
unnamed: STEPPER-3.1, STEPPER-3-CON.MOTORB-2
unnamed: STEPPER-3.2, STEPPER-3-CON.MOTORB-1
unnamed: STEPPER-3.3, STEPPER-3-CON.MOTORA-1
unnamed: STEPPER-3.4, STEPPER-3-CON.MOTORA-2
unnamed: R3.2, STATUS_LED.3 (GRN)
unnamed: R2.2, STATUS_LED.4 (BLU)
unnamed: R1.2, STATUS_LED.1 (RED)
unnamed: MAGNET.1, T1.E
PWRIN: POWER.1; also elsewhere on the board

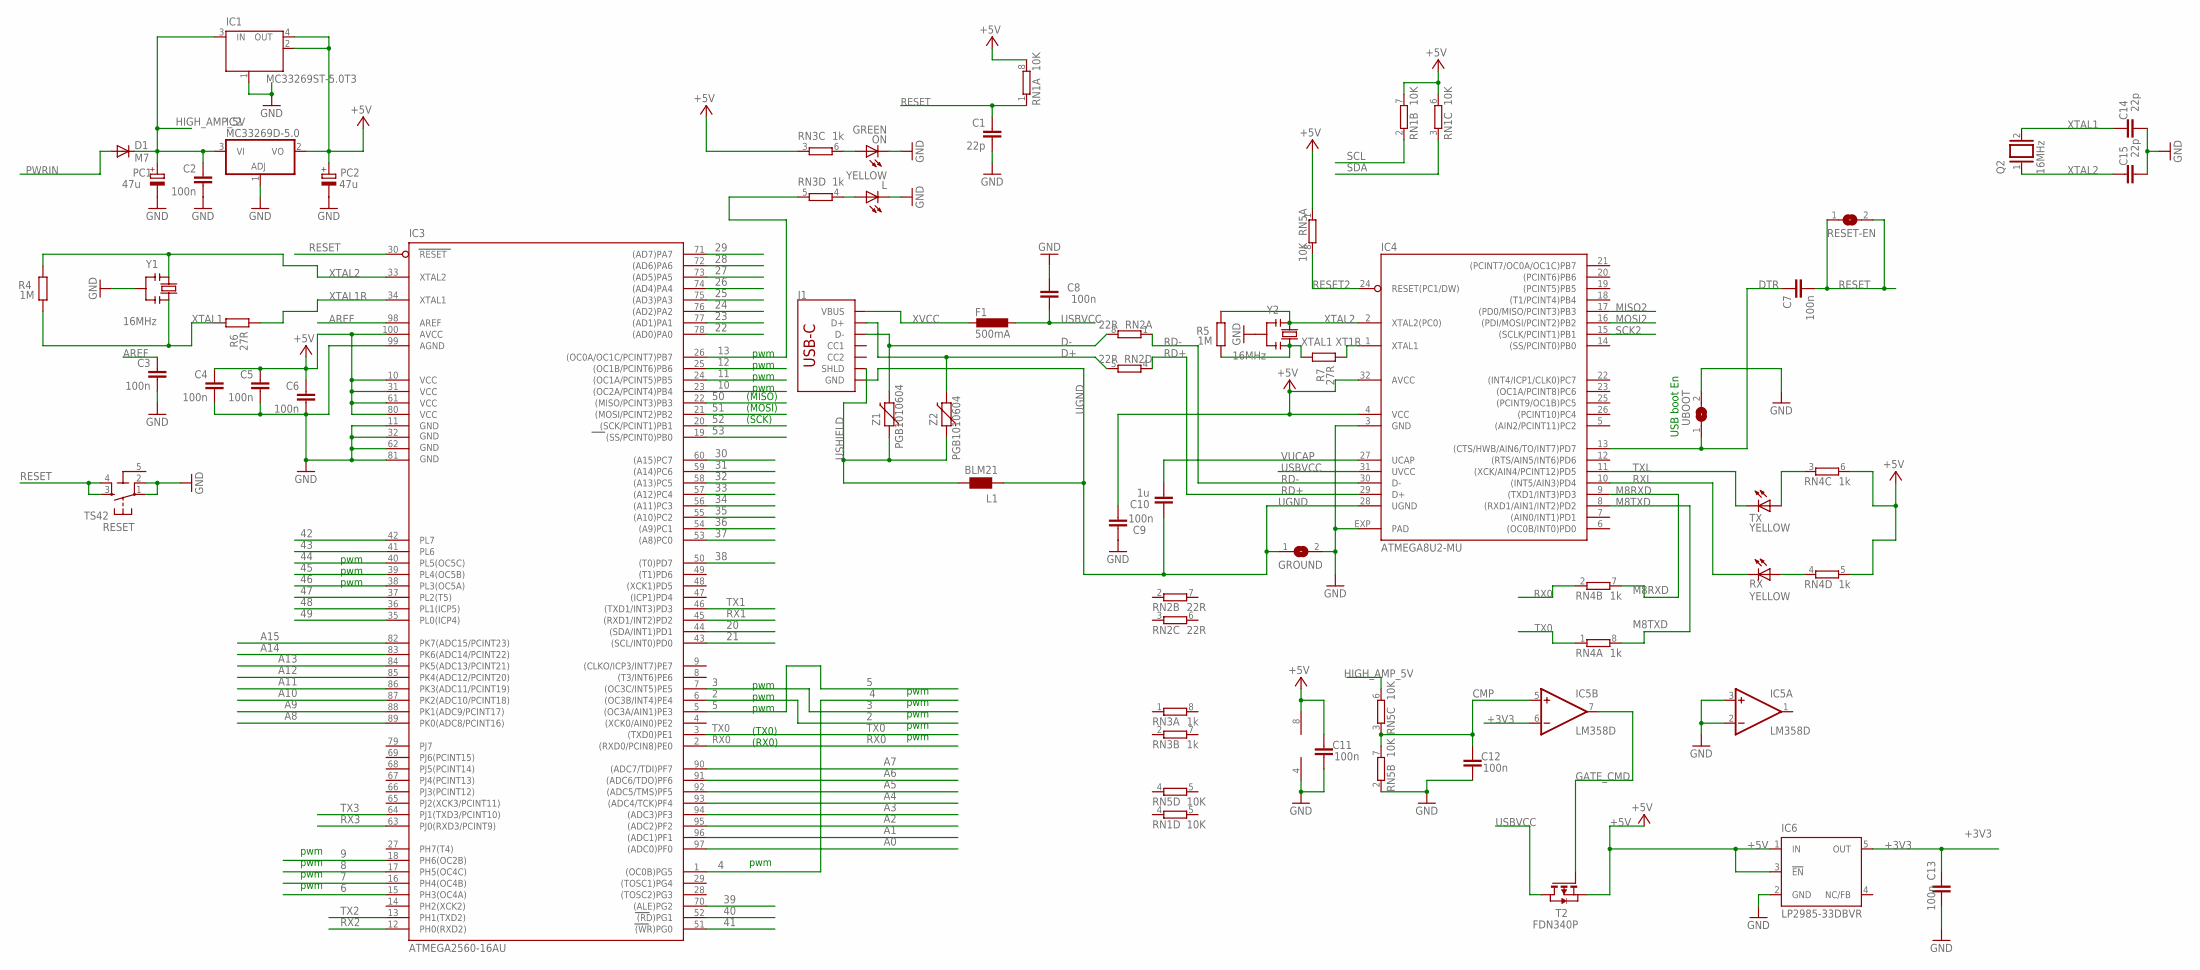
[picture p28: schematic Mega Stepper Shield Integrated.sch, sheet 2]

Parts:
C1, C14, C15: 22p; C0603-ROUND
C2, C3, C4, C5, C6, C7, C9, C12, C13: 100n; C0603-ROUND
C8, C11: 100n; C0603
C10: 1u; C0603-ROUND
D1: M7; SMB
F1: 500mA; L1812
GROUND: SJ
IC1: MC33269ST-5.0T3; SOT223
IC2: MC33269D-5.0; DPACK
IC3: ATMEGA2560-16AU; TQFP100
IC4: ATMEGA8U2-MU; QFN32
IC5: LM358D; SO08
IC6: LP2985-33DBVR; SOT23-DBV
J1: USB_C_2-LAYER_PADS; USB-C-16P-2LAYER-PADS
L: YELLOW; CHIP-LED0805
L1: BLM21; 0805
ON: GREEN; CHIP-LED0805
PC1, PC2: 47u; PANASONIC_D
Q2: 16MHz; QS
R4, R5: 1M; R0603-ROUND
R6, R7: 27R; R0603-ROUND
RESET: TS42
RESET-EN: SJ
RN1, RN5: 10K; CAT16
RN2: 22R; CAY16
RN3, RN4: 1k; CAY16
RX: YELLOW; CHIP-LED0805
T2: FDN340P; SOT-23
TX: YELLOW; CHIP-LED0805
UBOOT: SJ
Y1, Y2: 16MHz; RESONATOR
Z1, Z2: PGB1010604; CT/CN0603

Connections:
2: IC3.6 ((OC3B/INT4)PE4); also elsewhere on the board
3: IC3.7 ((OC3C/INT5)PE5); also elsewhere on the board
4: IC3.1 ((OC0B)PG5); also elsewhere on the board
5: IC3.5 ((OC3A/AIN1)PE3); also elsewhere on the board
5-GND: RESET.5 (5-GND)
6: IC3.15 (PH3(OC4A)); also elsewhere on the board
7: IC3.16 (PH4(OC4B)); also elsewhere on the board
8: IC3.17 (PH5(OC4C)); also elsewhere on the board
9: IC3.18 (PH6(OC2B)); also elsewhere on the board
10: IC3.23 ((OC2A/PCINT4)PB4); also elsewhere on the board
11: IC3.24 ((OC1A/PCINT5)PB5); also elsewhere on the board
12: IC3.25 ((OC1B/PCINT6)PB6); also elsewhere on the board
13: IC3.26 ((OC0A/OC1C/PCINT7)PB7), RN3.5 (2); also elsewhere on the board
20: IC3.44 ((SDA/INT1)PD1)
21: IC3.43 ((SCL/INT0)PD0)
22: IC3.78 ((AD0)PA0); also elsewhere on the board
23: IC3.77 ((AD1)PA1); also elsewhere on the board
24: IC3.76 ((AD2)PA2); also elsewhere on the board
25: IC3.75 ((AD3)PA3); also elsewhere on the board
26: IC3.74 ((AD4)PA4); also elsewhere on the board
27: IC3.73 ((AD5)PA5); also elsewhere on the board
28: IC3.72 ((AD6)PA6); also elsewhere on the board
29: IC3.71 ((AD7)PA7); also elsewhere on the board
30: IC3.60 ((A15)PC7); also elsewhere on the board
31: IC3.59 ((A14)PC6); also elsewhere on the board
32: IC3.58 ((A13)PC5); also elsewhere on the board
33: IC3.57 ((A12)PC4); also elsewhere on the board
34: IC3.56 ((A11)PC3); also elsewhere on the board
35: IC3.55 ((A10)PC2); also elsewhere on the board
36: IC3.54 ((A9)PC1); also elsewhere on the board
37: IC3.53 ((A8)PC0); also elsewhere on the board
38: IC3.50 ((T0)PD7); also elsewhere on the board
39: IC3.70 ((ALE)PG2); also elsewhere on the board
40: IC3.52 ((RD)PG1); also elsewhere on the board
41: IC3.51 ((WR)PG0); also elsewhere on the board
42: IC3.42 (PL7); also elsewhere on the board
43: IC3.41 (PL6); also elsewhere on the board
44: IC3.40 (PL5(OC5C)); also elsewhere on the board
45: IC3.39 (PL4(OC5B)); also elsewhere on the board
46: IC3.38 (PL3(OC5A)); also elsewhere on the board
47: IC3.37 (PL2(T5)); also elsewhere on the board
48: IC3.36 (PL1(ICP5)); also elsewhere on the board
49: IC3.35 (PL0(ICP4)); also elsewhere on the board
50: IC3.22 ((MISO/PCINT3)PB3); also elsewhere on the board
51: IC3.21 ((MOSI/PCINT2)PB2); also elsewhere on the board
52: IC3.20 ((SCK/PCINT1)PB1); also elsewhere on the board
53: IC3.19 ((SS/PCINT0)PB0)
+3V3: C13.2, IC5.6 (-IN), IC6.5 (OUT)
+5V: C4.1, C5.1, C6.1, C9.1, C11.2, IC1.2 (OUT), IC1.4 (OUT), IC2.2 (VO), IC3.10 (VCC), IC3.31 (VCC1), IC3.61 (VCC2), IC3.80 (VCC3), IC3.100 (AVCC), IC4.4 (VCC), IC4.32 (AVCC), IC5.8 (V+), IC6.1 (IN), IC6.3 (!EN), PC2.+, RN1.6 (2), RN1.7 (2), RN1.8 (2), RN3.3 (1), RN4.5 (2), RN4.6 (2), RN5.1, T2.2 (S); also elsewhere on the board
A0: IC3.97 ((ADC0)PF0); also elsewhere on the board
A1: IC3.96 ((ADC1)PF1); also elsewhere on the board
A2: IC3.95 ((ADC2)PF2); also elsewhere on the board
A3: IC3.94 ((ADC3)PF3); also elsewhere on the board
A4: IC3.93 ((ADC4/TCK)PF4); also elsewhere on the board
A5: IC3.92 ((ADC5/TMS)PF5); also elsewhere on the board
A6: IC3.91 ((ADC6/TDO)PF6); also elsewhere on the board
A7: IC3.90 ((ADC7/TDI)PF7); also elsewhere on the board
A8: IC3.89 (PK0(ADC8/PCINT16)); also elsewhere on the board
A9: IC3.88 (PK1(ADC9/PCINT17)); also elsewhere on the board
A10: IC3.87 (PK2(ADC10/PCINT18)); also elsewhere on the board
A11: IC3.86 (PK3(ADC11/PCINT19))
A12: IC3.85 (PK4(ADC12/PCINT20))
A13: IC3.84 (PK5(ADC13/PCINT21))
A14: IC3.83 (PK6(ADC14/PCINT22))
A15: IC3.82 (PK7(ADC15/PCINT23))
AREF: C3.1, IC3.98 (AREF)
CMP: C12.2, IC5.5 (+IN), RN5.3 (1), RN5.7 (2)
D+: J1.A6 (D+), J1.B6 (D+), RN2.5 (2), Z2.2
D-: J1.A7 (D-), J1.B7 (D-), RN2.8 (2), Z1.2
DTR: C7.1, IC4.13 ((CTS/HWB/AIN6/TO/INT7)PD7), UBOOT.1
GATE_CMD: IC5.7 (OUT), T2.3 (G)
GND: C1.2, C2.2, C3.2, C4.2, C5.2, C6.2, C8.2, C9.2, C11.1, C12.1, C13.1, C14.1, C15.1, GROUND.2, IC1.1 (GND/ADJ), IC2.1 (ADJ), IC3.11 (GND), IC3.32 (GND1), IC3.62 (GND2), IC3.81 (GND3), IC3.99 (AGND), IC4.3 (GND), IC4.EXP (PAD), IC5.2 (-IN), IC5.3 (+IN), IC5.4 (V-), IC6.2 (GND), L.C, ON.C, PC1.-, PC2.-, RESET.1, RESET.2, RN5.2 (1), UBOOT.2, Y1.2, Y2.2; also elsewhere on the board
HIGH_AMP_5V: C2.1, D1.C, IC1.3 (IN), IC2.3 (VI), PC1.+, RN5.6 (2); also elsewhere on the board
M8RXD: IC4.9 ((TXD1/INT3)PD3), RN4.7 (2)
M8TXD: IC4.8 ((RXD1/AIN1/INT2)PD2), RN4.8 (2)
MISO2: IC4.17 ((PD0/MISO/PCINT3)PB3)
MOSI2: IC4.16 ((PDI/MOSI/PCINT2)PB2)
unnamed: ON.A, RN3.6 (2)
unnamed: L.A, RN3.4 (1)
unnamed: RN4.4 (1), RX.A
unnamed: RN4.3 (1), TX.A
PWRIN: D1.A; also elsewhere on the board
RD+: IC4.29 (D+), RN2.4 (1)
RD-: IC4.30 (D-), RN2.1
RESET: C1.1, C7.2, IC3.30 (RESET), RESET.3, RESET.4, RESET-EN.1, RESET-EN.2, RN1.1
RESET2: IC4.24 (RESET(PC1/DW)), RN5.8 (2)
RX0: IC3.2 ((RXD0/PCIN8)PE0), RN4.2 (1)
RX1: IC3.45 ((RXD1/INT2)PD2)
RX2: IC3.12 (PH0(RXD2))
RX3: IC3.63 (PJ0(RXD3/PCINT9))
RXL: IC4.10 ((INT5/AIN3)PD4), RX.C
SCK2: IC4.15 ((SCLK/PCINT1)PB1)
SCL: RN1.2 (1)
SDA: RN1.3 (1)
TX0: IC3.3 ((TXD0)PE1), RN4.1
TX1: IC3.46 ((TXD1/INT3)PD3)
TX2: IC3.13 (PH1(TXD2))
TX3: IC3.64 (PJ1(TXD3/PCINT10))
TXL: IC4.11 ((XCK/AIN4/PCINT12)PD5), TX.C
UGND: C10.2, GROUND.1, IC4.28 (UGND), J1.GND, J1.GND2 (GND), L1.1
USBVCC: C8.1, F1.1, IC4.31 (UVCC), T2.1 (D)
USHIELD: J1.SHLD1 (SHLD), J1.SHLD2 (SHLD), J1.SHLD3 (SHLD), J1.SHLD4 (SHLD), L1.2, Z1.1, Z2.1
VUCAP: C10.1, IC4.27 (UCAP)
XT1R: IC4.1 (XTAL1), R7.1
XTAL1: C14.2, Q2.2, R4.1, R5.1, R6.2, R7.2, Y1.3, Y2.3
XTAL1R: IC3.34 (XTAL1), R6.1
XTAL2: C15.2, IC3.33 (XTAL2), IC4.2 (XTAL2(PC0)), Q2.1, R4.2, R5.2, Y1.1, Y2.1
XVCC: F1.2, J1.VBUS1 (VBUS), J1.VBUS2 (VBUS)

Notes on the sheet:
pwm
(TX0)
(RX0)
(MISO)
(SCK)
(MOSI)
USB boot En

Board: 2 copper layers, 70 parts (0 on the bottom side), 106 nets, no tracks yet.

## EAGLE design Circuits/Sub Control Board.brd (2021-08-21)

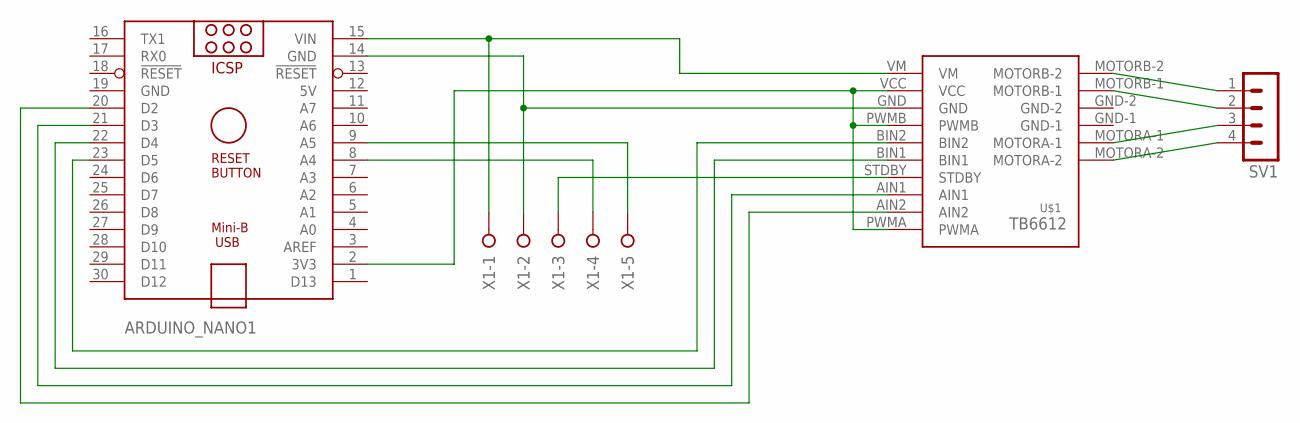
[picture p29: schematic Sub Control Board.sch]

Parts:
ARDUINO_NANO1: ARDUINO_NANO
SV1: MA04-1
U$1: TB6612-BREAKOUT-MOTOR-CONTROLLER; TB6612-HEADERS
X1: W237-05P; W237-5P

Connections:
5V: ARDUINO_NANO1.12 (5V)
GND: ARDUINO_NANO1.19 (GND)
unnamed: ARDUINO_NANO1.15 (VIN), U$1.VM, X1.1
unnamed: ARDUINO_NANO1.14 (GND), U$1.GND, X1.2
unnamed: U$1.STDBY, X1.3
unnamed: ARDUINO_NANO1.8 (A4), X1.4
unnamed: ARDUINO_NANO1.9 (A5), X1.5
unnamed: ARDUINO_NANO1.2 (3V3), U$1.PWMA, U$1.PWMB, U$1.VCC
unnamed: ARDUINO_NANO1.23 (D5), U$1.BIN2
unnamed: ARDUINO_NANO1.22 (D4), U$1.BIN1
unnamed: ARDUINO_NANO1.21 (D3), U$1.AIN1
unnamed: ARDUINO_NANO1.20 (D2), U$1.AIN2
unnamed: SV1.1, U$1.MOTORB-2
unnamed: SV1.2, U$1.MOTORB-1
unnamed: SV1.3, U$1.MOTORA-1
unnamed: SV1.4, U$1.MOTORA-2

Board: 2 copper layers, 4 parts (0 on the bottom side), 14 nets, no tracks yet.

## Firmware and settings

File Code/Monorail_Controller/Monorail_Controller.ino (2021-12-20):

/*-------------------------------------------------------------
                Project by Matthew Herber
                Concept by Nicholas Seward
-------------------------------------------------------------*/

//Include the neccesary librarys
#include <AccelStepper.h>

// Define some steppers and the pins the will use
AccelStepper stepper1(AccelStepper::FULL4WIRE, 22, 23, 24, 25);
AccelStepper stepper2(AccelStepper::FULL4WIRE, 26, 27, 28, 29);
AccelStepper stepper3(AccelStepper::FULL4WIRE, 30, 31, 32, 33);
//Extra Pin Definitions
int stepper1endstop = 34;
int stepper2endstop = 35;
int stepper3endstop = 36;
int ELECTROMAGNET = 37;

const int STEPPER_SHIFT_ANGLE = 70;	//this is the angle that the stepper mount is shifted by for vertical movement
const int MAX_SPEED = 700;
const int MAX_ACCEL = MAX_SPEED * 3;
const float MM_TO_STEP_RATIO = 0.25; //-0.75;	//This controls the ratio of steps to MM's
const int ZERO_SPEED = 250;	//how quickly should we zero the robot for initial position reset
const int PROGRAM_LINE_COUNT = 100;	//whats the maximum ammount of lines the program can be
const float ARCSPEED = 0.25; //how quickly to move during an arc command
String programList[PROGRAM_LINE_COUNT];	//maximum of 100 commands (changeable ofc, dynamic arrays arent a thing I wanted to implement here)
int lastArrayPoint = 0;	//used to know where we are in the listed program
int programCounter = 0;	//used to count what line we are on in the program
float percentSpeed = 1.0;

void setMotionAccel(int accel = MAX_ACCEL);

/*
Comments are available using #. Comments REQUIRE ';\' still as im lazy ;)

List of movement commands:
lmove(x,y,z)                       |Moves the robot EOAT to the specified X Y Z coordinates in a straight line|
jmove(x,y,z)                       |Moves the robot EOAT to the specified X Y Z coordinates as quick as possible|
delay(ms)                          |Halts program execution for a specified ammount of milliseconds|
speed(%)                           |Sets the speed of the robot based on a percentage of the max speed. This change affects all motion moves after it is called|
accel(%)                           |Sets the acceleration of the robot based on a percentage of the max acceleration. This change affects all motion moves after it is called|
Carc(x,y,z,r,startAngle,endAngle)  |Does a clockwise arc move given a center position, a radius from that center, a start angle and an end angle. always make sure your end angle is larger than your start angle|
CCarc(x,y,z,r,startAngle,endAngle) |Does a counter-clockwise arc move given a center position, a radius from that center, a start angle and an end angle. always make sure your end angle is larger than your start angle|

List of EOAT commands:
EOAT(T/F)                          |Turns on or off the EOAT, 0 for off and 1 for on|
*/
String program = "\
#basic starting program for testing;\
jmove(550,200,100);\
delay(1000);\
jmove(50,50,25);\
jmove(500,50,5);\
jmove(200,100,100);\
jmove(0,0,0);\
delay(1000);\
EOAT(1);\
;\
#Section to test speed command;\
speed(20);\
lmove(300,200,300);\
speed();\
lmove(0,0,0);\
EOAT(0);\
;\
#Section to test accel command;\
delay(1000);\
accel(5);\
lmove(300,200,300);\
accel();\
lmove(0,0,0);\
delay(1000);\
EOAT(1);\
#Rapid section testing individual axis moves;\
#X;\
lmove(200,0,0);\
delay(1000);\
jmove(100,0,0);\
#Y;\
lmove(100,100,0);\
delay(1000);\
jmove(100,0,0);\
#Z;\
lmove(100,0,100);\
delay(1000);\
jmove(100,0,0);\
#ALL AXIS;\
lmove(400,50,200);\
delay(1000);\
jmove(100,0,0);\
#Arc Testing;\
#Carc(400,200,0,200,360,0);\
lmove(0,0,0);\
#CCarc(400,200,0,200,0,360);\
lmove(0,0,0);\
EOAT(0);\
";

//This takes the program string and splits it into commands per line, putting it into programList
void splitProgram()
{
	while (program.indexOf(';') != -1)
	{
		programList[lastArrayPoint] = program.substring(0, program.indexOf(';'));
		program = program.substring(program.indexOf(';') + 1, program.length());
		lastArrayPoint++;
	}
}

void stringToArray(String *ar, String inputStr)
{
	int r = 0, t = 0;

	for (int i = 0; i < inputStr.length(); i++)
	{
		if (inputStr.charAt(i) == ',' || inputStr.charAt(i) == ')')
		{
			ar[t] = inputStr.substring(r, i);
			r = (i + 1);
			t++;
		}
	}
}

//This takes a single line command and figures out what it means and where to send input values, if any
void parseCommand(String command)
{
	//Comment Handling
	if (command.indexOf("#") != -1)
	{
		//do nothing :)
		return;
	}

	//Motion Commands
	else if (command.indexOf("lmove") != -1)
	{
		//Serial.println(command);
		String valueset = command.substring(command.indexOf("(") + 1);
		String values[3];
		stringToArray(values, valueset);
		int x = values[0].toInt();
		int y = values[1].toInt();
		int z = values[2].toInt();
		lmoveToCoordinates(x, y, z);
	}
	else if (command.indexOf("jmove") != -1)
	{
		//Serial.println(command);
		String valueset = command.substring(command.indexOf("(") + 1);
		String values[3];
		stringToArray(values, valueset);
		int x = values[0].toInt();
		int y = values[1].toInt();
		int z = values[2].toInt();
		jmoveToCoordinates(x, y, z);
	}
	else if (command.indexOf("CCarc") != -1)
	{
		String valueset = command.substring(command.indexOf("(") + 1);
		String values[6];
		stringToArray(values, valueset);
		int x = values[0].toInt();
		int y = values[1].toInt();
		int z = values[2].toInt();
		int r = values[3].toInt();
		int sangle = values[4].toInt();
		int eangle = values[5].toInt();
		arcmoveCC(x, y, z, r, sangle, eangle);
	}
	else if (command.indexOf("Carc") != -1)
	{
		String valueset = command.substring(command.indexOf("(") + 1);
		String values[6];
		stringToArray(values, valueset);
		int x = values[0].toInt();
		int y = values[1].toInt();
		int z = values[2].toInt();
		int r = values[3].toInt();
		int sangle = values[4].toInt();
		int eangle = values[5].toInt();
		arcmoveC(x, y, z, r, sangle, eangle);
	}
	else if (command.indexOf("speed()") != -1)
	{
		//Serial.println(command);
		percentSpeed = 1.0;
	}
	else if (command.indexOf("speed") != -1)
	{
		//Serial.println(command);
		String valueset = command.substring(command.indexOf("(") + 1);
		String values[1];
		stringToArray(values, valueset);
		percentSpeed = values[0].toInt() / 100.0;
	}
	else if (command.indexOf("accel()") != -1)
	{
		//Serial.println(command);
		setMotionAccel(MAX_ACCEL);	//Reset motion accel to max
	}
	else if (command.indexOf("accel") != -1)
	{
		//Serial.println(command);
		String valueset = command.substring(command.indexOf("(") + 1);
		String values[1];
		stringToArray(values, valueset);
		setMotionAccel((values[0].toInt() / 100.0) *MAX_ACCEL);	//find the value in the command, then divide it by 100 and multiply it by MAX_ACCEL
	}

	//Time Commands
	if (command.indexOf("delay") != -1)
	{
		//Serial.println(command);
		String valueset = command.substring(command.indexOf("(") + 1);
		String values[1];
		stringToArray(values, valueset);
		delay(values[0].toInt());
	}

  //EOAT Commands
  if (command.indexOf("EOAT") != -1)
  {
    String valueset = command.substring(command.indexOf("(") + 1);
    String values[1];
    stringToArray(values, valueset);
    energizeMagnet(values[0].toInt());
  }
}

void setup()
{
	pinMode(stepper1endstop, INPUT);
	pinMode(stepper2endstop, INPUT);
	pinMode(stepper3endstop, INPUT);
  pinMode(ELECTROMAGNET, OUTPUT); //Set electromagnet pin to output
	setMotionAccel();
	//Serial.begin(9600);
	splitProgram();
	//Initial test move
	reZero();
	jmoveToCoordinates(0, 0, 0);
}

void loop()
{
	stepper1.run();
	stepper2.run();
	stepper3.run();

 
	//if we have reached the position we are trying to move to, we have finished a line and should move to the next line in the program
	if (stepper1.distanceToGo() == 0 && stepper2.distanceToGo() == 0 && stepper3.distanceToGo() == 0)
	{
		parseCommand(programList[programCounter]);
		programCounter++;
	}

	//if we reach the end of the program, go into an infinite loop to stop execution
	if (programCounter == PROGRAM_LINE_COUNT && true)
	{
		//Serial.println("Program Complete!");
		//while(true);	//stop execution by getting stuck in a infinite loop
		programCounter = 0;
	}
}

void moveToCoordinates(float x, float y, float z)
{
	//initial offsets to cart position offsets
	//x = x + 140;
	//y = y + 180;
	//z = 580 - z;

  float stepper1calc = (x - z) / MM_TO_STEP_RATIO;
  float stepper2calc = (x - (y* tan(radians(90 - STEPPER_SHIFT_ANGLE)))) / MM_TO_STEP_RATIO;
  float stepper3calc = (x + z) / MM_TO_STEP_RATIO;

  //if any of the calculated stepper positions return a negative stepper location, error out
  if (stepper1calc < 0 || stepper2calc < 0 || stepper3calc < 0) {
    while (true){
      //infinite loop
    }
  }

	stepper1.moveTo(stepper1calc);
	stepper2.moveTo(stepper2calc);
	stepper3.moveTo(stepper3calc);
}

void lmoveToCoordinates(float x, float y, float z)
{
	moveToCoordinates(x, y, z);
	//abs all of these as we just want the distance, not the direction
	long s1d = abs(stepper1.distanceToGo());
	long s2d = abs(stepper2.distanceToGo());
	long s3d = abs(stepper3.distanceToGo());
	float MaxDistance = max(s1d, s3d);

	float VectorMultiplier = 1.0 / MaxDistance;
	if (s1d == 0 && s3d == 0) { VectorMultiplier = 1.0 / s2d; }	//account for the fact that if both exterior carriages dont move, we will calc NaN for vector multiplier

	stepper1.setMaxSpeed((VectorMultiplier *s1d) *MAX_SPEED *percentSpeed);
	stepper2.setMaxSpeed((VectorMultiplier *s2d) *MAX_SPEED *percentSpeed);
	stepper3.setMaxSpeed((VectorMultiplier *s3d) *MAX_SPEED *percentSpeed);
}

void jmoveToCoordinates(float x, float y, float z)
{
	moveToCoordinates(x, y, z);
	stepper1.setMaxSpeed(MAX_SPEED *percentSpeed);
	stepper2.setMaxSpeed(MAX_SPEED *percentSpeed);
	stepper3.setMaxSpeed(MAX_SPEED *percentSpeed);
}

void arcmoveCC(float x, float y, float z, float r, float sAngle, float eAngle)
{
  float calcXpos = (r* cos(radians(sAngle))) + x;
  float calcYpos = (r* sin(radians(sAngle))) + y;
  jmoveToCoordinates(calcXpos,calcYpos,z);
  float prevpercentSpeed = percentSpeed;
  percentSpeed = ARCSPEED;
	for (int angle = sAngle; angle < eAngle; angle += 15)
	{
		calcXpos = (r* cos(radians(angle))) + x;
		calcYpos = (r* sin(radians(angle))) + y;
		lmoveToCoordinates(calcXpos, calcYpos, z);
		while (stepper1.distanceToGo() != 0 && stepper2.distanceToGo() != 0 && stepper3.distanceToGo() != 0)
		{
			stepper1.run();
			stepper2.run();
			stepper3.run();
		}
	}
 percentSpeed = prevpercentSpeed;
}

void arcmoveC(float x, float y, float z, float r, float sAngle, float eAngle)
{
  float calcXpos = (r* cos(radians(sAngle))) + x;
  float calcYpos = (r* sin(radians(sAngle))) + y;
  jmoveToCoordinates(calcXpos,calcYpos,z);
  float prevpercentSpeed = percentSpeed;
  percentSpeed = ARCSPEED;
	for (int angle = sAngle; angle > eAngle; angle -= 15)
	{
		calcXpos = (r* cos(radians(angle))) + x;
		calcYpos = (r* sin(radians(angle))) + y;
		lmoveToCoordinates(calcXpos, calcYpos, z);
		while (stepper1.distanceToGo() != 0 && stepper2.distanceToGo() != 0 && stepper3.distanceToGo() != 0)
		{
			stepper1.run();
			stepper2.run();
			stepper3.run();
		}
	}
	percentSpeed = prevpercentSpeed;
}

void setMotionAccel(int accel)
{
	stepper1.setAcceleration(accel);
	stepper2.setAcceleration(accel);
	stepper3.setAcceleration(accel);
}

void energizeMagnet(int control)
{
  switch(control){
    case 0:
    {
      digitalWrite(ELECTROMAGNET, LOW); //Disable the Electromagnet
      break;
    }
    case 1:
    {
      digitalWrite(ELECTROMAGNET, HIGH); //Enable the Electromagnet
      break;
    }
  }
}

void reZero()
{
  //set the speed of the motors to a slow accurate speed for initial hardware zeroing
	stepper1.setSpeed(ZERO_SPEED);
	stepper2.setSpeed(ZERO_SPEED);
	stepper3.setSpeed(ZERO_SPEED);

  //Keep running till all three endstops are triggered
	while (digitalRead(stepper1endstop) == LOW || digitalRead(stepper2endstop) == LOW || digitalRead(stepper3endstop) == LOW)
	{
		if (digitalRead(stepper1endstop) == LOW)
		{
      stepper1.move(-1);
			stepper1.runSpeedToPosition();
		}

		if (digitalRead(stepper2endstop) == LOW)
		{
      stepper2.move(-1);
			stepper2.runSpeedToPosition();
		}

		if (digitalRead(stepper3endstop) == LOW)
		{
      stepper3.move(-1);
			stepper3.runSpeed();
		}
	}

  int offset = -20;
  //Register the current position of the steppers as the new zero
  stepper1.setCurrentPosition(offset);
  stepper2.setCurrentPosition(offset);
  stepper3.setCurrentPosition(offset);
}

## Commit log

2021-05-04 Initial commit including current source code
2021-05-04 Commit to sync to HDD
    Added CAD and circuit board schematic
    [060_30_1_1.stp, 060_30_2_2.stp, 0_195m_Z045_16_018_0_1.stp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]
2021-05-04 Re Organization of file structure
    [Bar.SLDPRT, Drag Chain Static Mount.SLDPRT, Head.SLDPRT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]
2021-05-04 Fixed arduino sketchbook
2021-05-04 Changed to correct EAGLE files from laptop
    [3 Stepper Shield.brd, 3 Stepper Shield.sch, Mega Stepper Shield.brd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]
2021-05-04 Update Drive gear to have D shaft
    [5172T160_HT-LOAD MTL GEAR--20 DEG PRESSURE ANGLE.SLDPRT, Drive Gear.STL]
2021-05-04 Updated Code and Model
    [Slide Casing.SLDPRT]
2021-05-06 Edited Gear Rack to include mounting holes
    [5174T110_HT-LOAD MTL GEAR RACK--20 DEG PRESSURE ANGLE.SLDPRT]
2021-05-07 Fixed Discrepancy between purchased parts and cad
    Also redid the slide casings to work and be simple in order for testing
    [Slide Casing.SLDPRT, Test Slide Casing.STL, V-Slot Gantry Kit - 20mm.step]
2021-05-07 Add alternative smaller spur gear incase torque is an issue
    [5172T160_HT-LOAD MTL GEAR--20 DEG PRESSURE ANGLE.SLDPRT, 5172T560_HIGH-LOAD METAL GEAR - 20 DEG PRESSURE ANGLE.SLDPRT]
2021-05-08 Temporary Rack mount
    [Temporary Gear Mount.SLDPRT, Temporary Gear Mount.STL]
2021-05-10 Managed to create an engineering render
    Calculates the positions, the only thing missing is the arms themselves, as that would require bones and IK
    [Carriage.PLY, Extrusion.PLY, Gear Rack.PLY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]
2021-05-10 Added calculation to make steppers all arrive at the same time
2021-05-10 Slowed down due to mechanical instability causing skipped steps
    This isnt an issue when finished (atleast to my knowledge) as when this is built correctly it will be using screws, not zipties. the zipties are allowing it to resonate quite badly
    [Monorail_Controller.ino]
2021-05-12 slight changes to model
    [Slide Casing.SLDPRT, Temporary Gear Mount.SLDPRT, Temporary Gear Mount.STL]
2021-05-12 Update stored Program and flipped drive direction
    [Temporary Gear Mount.SLDPRT, Temporary Gear Mount.STL]
2021-05-13 Tweaked MM ratio, added L and J moves and fixed bug with linear move code
    [Monorail_Controller.ino]
2021-05-14 Bearing Fit test files
    [Bar.SLDPRT, Bearing Fit Test Internal.SLDPRT, Bearing Fit Test Internal.STL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]
2021-05-14 Arc commands Depreciated for now as they do not function
    Come back to later. unsure why broke
    [Monorail_Controller.ino]
2021-05-14 Fixed bug with stepper 2 location.
    Was sending in degrees into tan() when the format should be radians
    [Monorail_Controller.ino]
2021-05-14 Add Circuits to gitattributes
2021-05-15 Fixed Arc Commands and overall stability improvements
    [Monorail_Controller.ino]
2021-05-16 bearing design for bar and improvements to head file
    [Bar.SLDPRT, Bar.STL, Bearing Fit Test Internal.SLDPRT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]
2021-05-16 Updated Head part to include bearings, and reduced weight
    [Bar.SLDPRT, Head.SLDPRT, Outer Mounts Default.STL]
2021-05-17 Attempted improvements to bars and fixed head
    [Bar.SLDPRT, Head.SLDPRT, Head.STL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]
2021-05-18 create a split version of the arms
    [Bar Assembled.SLDASM, Bar.SLDPRT, Outer Mounts.SLDPRT]
2021-05-18 Add generated STL files
    [Bar Female.STL, Bar Male.STL]
2021-08-06 Update CAD and Program
    Added EOAT commands
    Added stand to CAD
    [20_2020_Black_381_CL.sldprt, 20_2020_Black_609_6_CL.sldprt, 20_2040_Black_1219_2_CL.sldprt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]
2021-08-11 Buncha Code Fixes
    Fixed negative MM step value
    Added error out on negative stepper positions
    Zeroing now offsets after endstop hit
    [Monorail_Controller.ino]
2021-08-20 Update CAD
    [Bar Assembled.SLDASM, Bus Bar Concept.SLDASM, Bus Bar Holder.SLDPRT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]
2021-08-21 Update schematic and prototype schematic
    Added RF module to schematic, created a prototype sub board for multiple stepper control
    [20_2020_Black_609_6_CL.sldprt, 20_2040_Black_1219_2_CL.sldprt, 20_4113_Black.sldprt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]
2021-08-21 Add Light Stack and CAD Materials
    Added custom lightstack and custom materials to fix the density of printed parts. Also cleaned up the main assembly tree into folders
    [5172T160_HT-LOAD MTL GEAR--20 DEG PRESSURE ANGLE.SLDPRT, Aluminum Bar Wire.DXF, Aluminum Bar.SLDPRT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]
2021-08-23 Update Board Design
    [Mega Stepper Shield.brd, Mega Stepper Shield.sch]
2021-08-26 Update Board
    Added SPI Bus, changed symbol for SD Card Breakout, changed board layout
    [Mega Stepper Shield.brd, Mega Stepper Shield.sch]
2021-08-27 Update Circuit and include electrical mount
    [20_2040_Black_1219_2_CL.sldprt, Board Mount.SLDPRT, Board.SLDASM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]
2021-08-28 Changes to improve Flexibility
    [Board.SLDASM, Electromagnet EOAT.SLDPRT, FEA Assembly.SLDASM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]
2021-08-31 Create Integrated Version of Board
    [Mega Stepper Shield Integrated.brd, Mega Stepper Shield Integrated.sch, Mega Stepper Shield.brd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]
2021-08-31 Improve CAD to reduce Backlash
    [Board.SLDASM, Cart Limit Flag.SLDPRT, Electromagnet EOAT.SLDPRT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]
2021-08-31 Tool Changer Mockup
    [ATC Example Usage.SLDASM, ATC Tool Holder.SLDPRT, ATC Tool Mount.SLDPRT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]
2021-11-01 Re Added Non integrated board design
    Realized I removed these when updating the boards to an integrated version
    [Mega Stepper Shield.brd, Mega Stepper Shield.sch]
2021-12-17 Redesign 4.0
    Change Carts to cut plates
    Change motion to bearing solution from bushings
    lots of other fixes
    [20_2020_Black_609_6_CL.sldprt, 20_2040_Black_1219_2_CL.sldprt, 20_4113_Black.sldprt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]
2021-12-17 Remove Smart Fasteners
    Smart Fasteners werent coming in right on a different machine
    [Bar Assembled.SLDASM, Cart.SLDASM]
2021-12-17 Change layout of bearings to half count
    [Aluminum Bar.SLDPRT, Bar Assembled.SLDASM, Bar Clevis Plate.SLDPRT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]
2021-12-17 Fix folder structure and part naming
    [1_2 OD Hex Stock (18) (217-3309).step, 6627T67_Position-Control DC Motor.SLDPRT, 91780A212_Female Threaded Hex Standoff.SLDPRT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]
2021-12-17 remove unneccesary processing folder/files
    [Slide.STL, Slide.obj, Test.STL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]
2021-12-17 Fix Git Ignore and update Materials
    [A201 Cart Mount Plate.SLDPRT, A202 Cart Stepper Plate.SLDPRT, A203 Inner Mount Angle Bracket.SLDPRT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]
2021-12-17 Fix Gear Rack Height
    [A200 Cart.SLDASM, Temporary Gear Mount.SLDPRT]
2021-12-17 Fix Cart Endstop Peg Height
    [A200 Cart.SLDASM, A201 Cart Mount Plate.SLDPRT]
2021-12-17 Update Hex Size and insert hex hardware
    Not fully done with this commit-TBF
    [A200 Cart.SLDASM, A204 Outer Mount Bearing Plate.SLDPRT, A400 Link.SLDASM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]
2021-12-20 Sync Files from laptop
    Missed brd changes and code changes for speed
    [Monorail_Controller.ino]

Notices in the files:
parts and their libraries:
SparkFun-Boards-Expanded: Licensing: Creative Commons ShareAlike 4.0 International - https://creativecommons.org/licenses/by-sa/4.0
